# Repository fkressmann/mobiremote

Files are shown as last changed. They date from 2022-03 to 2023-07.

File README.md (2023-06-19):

# MobiRemote

## What

This small tool was built to remote control and monitor a Mobicool FR 40 / MCF 40 (34/60
respectively) fridge. It's somehow inspired
by [this project on GitHub](https://github.com/UnifiedEngineering/mobicool-fr34) which completly
replaces the firmware of the controller. I didn't want to go that far to write my own firmware, I
just wanted the possibility of remote monitoring / control.

## Why

This project is part of my bigger SmartBoat project. I wanted to be able to integrate the fridge and
control the target temperature and on/off state (not just using a relay to turn off power). There
were two main reasons why I wanted to programmatically change the temp:

- According to the outside temperature (nobody needs 2°C beer at 30° outside temp, brain freeze
  coming...)
- The available electrical energy. Cool down during the day when there is a lot of PV energy. Save
  energy and noise at night. Rise temperature / turn off fridge when battery is low.

## How

As the internal logic of the fridge already runs on 3v3, I could use this for the ESP, too.

### Networking

MQTT is used for communication.

#### MQTT out

- ```{prefix}/ip``` IP address of the chip (retained)
- ```{prefix}/rssi``` Signal strength of the WiFi (retained)
- ```{prefix}/log``` Log (retained)
- ```{prefix}/temp``` Current temperature every 1-2sek
- ```{prefix}/target``` Reports back target temperature if set sucessfully
- ```{prefix}/power``` Reports back target temperature if set sucessfully

#### MQTT in

All settings require a number as payload

- ```{prefix}/cmnd/inittemp``` Set current target temperature (only for initialization)
- ```{prefix}/cmnd/initpower``` Set current power state (only for initialization)
- ```{prefix}/cmnd/target``` Set target temperature
- ```{prefix}/cmnd/power``` Set power state (turn on/off fridge)
- ```{prefix}/cmnd/status``` Output all configuration. Payload doesn't matter as long as it's specified

### Pressing buttons

I took the minimum invasive way and automated the four buttons of the fridges control panel using an
optocoupler for each button to simulate button presses. After playing a little with the timing, this
works very good by now. As the software is not getting any feedback of the controller, it needs to
remember the current target temperature. This is why it gets written to the flash after each
change (and loaded on boot, same for the power state). It's not planned to change the temperature
manually from now on.

In the beginning I thought about hijacking the SPI like communication between display panel and main
controller but after hooking up a logic analyser, this seemed too complex. Optocouplers are the
easiest way because the display chip (TM1620B) does some crazy multiplexing on the button inputs.
Didn't want so spend too much time reverse engineering that.

### Measuring temp

<del>
Furthermore, I realized that the fridge uses a 10k NTC for temperature measurement and connected
this one to the ESP, too to measure the inside temperature (previously, I had a DS18B20 inside and a
ribbon cable to through the lid).

Normally, you would use a Steinhart and Hart equation to calculate the temp from the resistance of
the NTC, but this somehow did not work out. So I decided to hook up two DS18B20 sensors, cool the
fridge down to -10°C and let it warm up slowly overnight while logging the mean temp of both
DS18B20 and the ESPs avg voltage reading of 1k samples (beware, read ADC only every 10ms or so,
otherwise WiFi crashes...). After plotting this, the curve was surprisingly linear. So used a linear
approximation which had a error of <0.2°C between 0 and 10°C. Precise enough I'd say :D

I did not disconnect the ADC from the main controller because it is used for controlling the
compressor. Maybe this is the reason why the measured voltage was so far off from what one would
expect from a 10k NTC. Nobody knows exactly what kind of voltage divider Mobicool uses on the main
board.
</del>

Forget this, this is for whatever reason way to unreliable. I ended up mounting a DS18B20 inside the box, using flex 
cables to pass through the hinge and ran wires through the cooling holes. Works way better now.

## Result
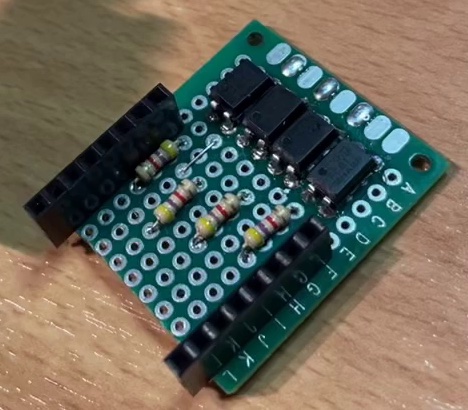
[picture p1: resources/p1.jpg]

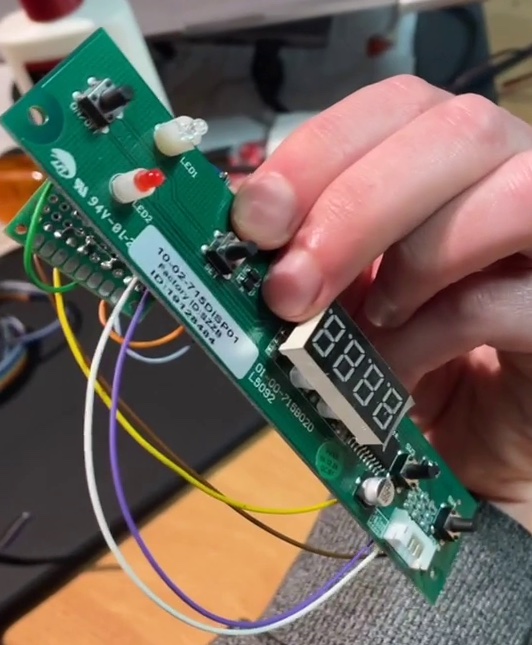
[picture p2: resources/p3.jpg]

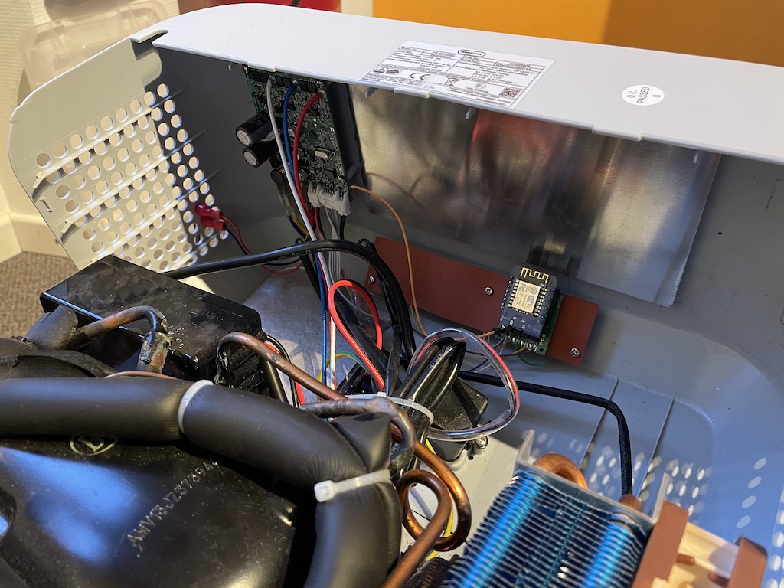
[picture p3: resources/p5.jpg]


## ToDo

- [x] Calibrate temp measurements
- [x] Send temp only when changed
- [x] Use WiFi manager instead of fixed WiFi credentials
- [x] Use WiFi manager to set mqtt settings
- [x] Add some pics here

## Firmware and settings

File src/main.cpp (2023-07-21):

#include <Arduino.h>
#include <ArduinoOTA.h>
#include <EEPROM.h>
#include <ESP8266WiFi.h>
#include <WiFiManager.h>
#include <PubSubClient.h>
#include <OneWire.h>
#include <DallasTemperature.h>
#include <credentials.h>

#define MCF_POWER D6
#define MCF_SET D7
#define MCF_UP D2
#define MCF_DOWN D3
#define BUTTON D5
#define ONE_WIRE_BUS D1
#define LED D4

#define MQTT_SERVER_LABEL "mq_server"
#define MQTT_USER_LABEL "mq_user"
#define MQTT_PASSWORD_LABEL "mq_pw"
#define MQTT_PREFIX_LABEL "mq_pref"

volatile boolean saveConfig = false;
volatile boolean buttonPressed = false;

const char *deviceName = "esp-mobiremote";

const char *topicPower = "power";
const char *topicTargetTemp = "target";
const char *topicIsTemp = "temp";
const char *topicInitTemp = "inittemp";
const char *topicInitPower = "initpower";
const char *topicStatus = "status";

float prevTemp = 0;
struct {
  int tempSet;
  boolean powerState;
  char mqttServer[30];
  char mqttUser[30];
  char mqttPassword[30];
  char mqttPrefix[30];
} config;
String commandPrefix;

WiFiManager wifiManager;

WiFiClient wifiClient;
PubSubClient mqttClient(wifiClient);

OneWire oneWire(ONE_WIRE_BUS);
DallasTemperature DS18B20(&oneWire);

void sendData(String subtopic, String data, bool retained) {
  Serial.println("SENDING: " + subtopic + ":" + data);
  subtopic = config.mqttPrefix + subtopic;
  mqttClient.publish(subtopic.c_str(), data.c_str(), retained);
}

void log(String line) {
  sendData("log", line, true);
}

void sendCurrentTargetTemp() {
    sendData(topicTargetTemp, String(config.tempSet), false);
}

void sendCurrentPowerState() {
    sendData(topicPower, String(config.powerState), false);
}

void sendCurrentTemperature() {
    sendData(topicIsTemp, String(prevTemp), false);
}

void writeConfigToEeprom() {
  EEPROM.begin(sizeof(config));
  EEPROM.put(0, config);
  EEPROM.commit();
  EEPROM.end();
  log("Config " + String(config.tempSet) + ":" + String(config.powerState) + " written to flash.");
}

void reconnectMqtt() {
  if (!mqttClient.connected()) {
    Serial.print("Attempting MQTT connection...");
    // Attempt to connect
    // if you MQTT broker has clientID,username and password
    // please change following line to    if (client.connect(clientId,userName,passWord))
    if (mqttClient.connect(deviceName, config.mqttUser, config.mqttPassword)) {
      Serial.println("connected");
      Serial.println("Subscribing to: " + commandPrefix);
      mqttClient.subscribe((commandPrefix + "/#").c_str());
      sendData("ip", WiFi.localIP().toString(), true);
      sendData("rssi", String(WiFi.RSSI()), true);
    } else {
      Serial.print("failed, rc=");
      Serial.print(mqttClient.state());
      Serial.println(" try again in 1 second");
      delay(1000);
    }
  }
}

void pressButton(int button, boolean longPress) {
  log("Pressing Button " + String(button));
  digitalWrite(button, HIGH);
  delay(200);
  if (longPress) delay(3000);
  digitalWrite(button, LOW);
  delay(100);
}

void pressButton(int button) {
  pressButton(button, false);
}

void changeSetTemperature(int delta) {
  if (delta == 0) {
    return;
  }
  pressButton(MCF_SET);
  if (delta < 0) {
    for (int i = 0; i > delta; i--) {
      pressButton(MCF_DOWN);
    }
  } else {
    for (int i = 0; i < delta; i++) {
      pressButton(MCF_UP);
    }
  }
  // wait for mobicool to exit temperature menu before doing anything else
  delay(11000);
}

void handleNewSetTemp(int newSetTemp) {
  if (!config.powerState) {
    log("Cannot set temp, mobicool is off");
    return;
  }
  if (newSetTemp == config.tempSet || newSetTemp < -10 || newSetTemp > 10) {
    log("Bad newTemp: " + String(newSetTemp) + " (oldTemp: " + String(config.tempSet) + ")");
    return;
  }
  int delta = newSetTemp - config.tempSet;
  changeSetTemperature(delta);
  config.tempSet = newSetTemp;
  writeConfigToEeprom();
  sendCurrentTargetTemp();
}

void handleNewPowerState(boolean newState) {
  if (config.powerState == newState) {
    log("Power is already " + String(newState));
  } else {
    pressButton(MCF_POWER, true);
    config.powerState = newState;
    writeConfigToEeprom();
  }
  sendCurrentPowerState();
}

void handleNtc() {
  DS18B20.requestTemperatures();
  float temp = DS18B20.getTempCByIndex(0);
  if (abs(temp - prevTemp) >= 0.1) {
    prevTemp = temp;
    sendCurrentTemperature();
  }
}

void sendInvalidCommandMessage(char *slashPointer, char *pl) {
  log("Invalid command: " + String(slashPointer) + ":" + String(pl));
}

void callback(char *topic, byte *payload, unsigned int length) {
  digitalWrite(LED, LOW);

  // Parse payload to c string
  char pl[length + 1];
  for (unsigned int i = 0; i < length; i++) {
    pl[i] = payload[i];
  }
  pl[length] = '\0';
  int plInt = atoi(pl);

  char *slashPointer = strrchr(topic, '/');
  if (length == 0) {
    sendInvalidCommandMessage(slashPointer, pl);
  }

  if (strcmp(slashPointer + 1, topicTargetTemp) == 0) {
    handleNewSetTemp(plInt);
  } else if (strcmp(slashPointer + 1, topicInitTemp) == 0) {
    config.tempSet = plInt;
    writeConfigToEeprom();
    sendCurrentTargetTemp();
  } else if (strcmp(slashPointer + 1, topicInitPower) == 0) {
    config.powerState = plInt;
    writeConfigToEeprom();
    sendCurrentPowerState();
  } else if (strcmp(slashPointer + 1, topicPower) == 0) {
    handleNewPowerState(plInt);
  } else if (strcmp(slashPointer + 1, topicStatus) == 0) {
    sendCurrentTemperature();
    sendCurrentTargetTemp();
    sendCurrentPowerState();
  } else {
    sendInvalidCommandMessage(slashPointer, pl);
  }
  digitalWrite(LED, HIGH);
}

void startConfigPortal() {
  WiFi.disconnect();
  ESP.restart();
}

void IRAM_ATTR buttonIsr() {
  buttonPressed = true;
}

void setup() {
  Serial.begin(115200);
  Serial.println();

  attachInterrupt(digitalPinToInterrupt(BUTTON), buttonIsr, FALLING);

  // Read settings from EEPROM
  EEPROM.begin(sizeof(config));
  EEPROM.get(0, config);
  EEPROM.end();
  log("Config " + String(config.tempSet) + ":" + String(config.powerState) + " loaded from flash.");
  Serial.printf("MQTT server: %s \n", config.mqttServer);
  Serial.printf("MQTT user: %s \n", config.mqttUser);
  Serial.printf("MQTT password: %s \n", config.mqttPassword);
  Serial.printf("MQTT prefix: %s \n", config.mqttPrefix);

  WiFi.hostname(deviceName);
  WiFi.persistent(true);

  WiFiManagerParameter p_mqttServer(MQTT_SERVER_LABEL, "MQTT Server", config.mqttServer, 30);
  wifiManager.addParameter(&p_mqttServer);
  WiFiManagerParameter p_mqttUser(MQTT_USER_LABEL, "MQTT User", config.mqttUser, 30);
  wifiManager.addParameter(&p_mqttUser);
  WiFiManagerParameter p_mqttPassword(MQTT_PASSWORD_LABEL, "MQTT Password", config.mqttPassword, 30);
  wifiManager.addParameter(&p_mqttPassword);
  WiFiManagerParameter p_mqttPrefix(MQTT_PREFIX_LABEL, "MQTT Prefix", config.mqttPrefix, 30);
  wifiManager.addParameter(&p_mqttPrefix);

  wifiManager.setConfigPortalTimeout(60);
  
  wifiManager.setSaveConfigCallback([]() {
    Serial.println("Should save config");
    saveConfig = true;
  });

  boolean connected = false;
  while (!connected) {
    connected = wifiManager.autoConnect(STA_SSID, STA_PSK);
  }
  if (saveConfig) {
    strcpy(config.mqttServer, p_mqttServer.getValue());
    strcpy(config.mqttUser, p_mqttUser.getValue());
    strcpy(config.mqttPassword, p_mqttPassword.getValue());
    strcpy(config.mqttPrefix, p_mqttPrefix.getValue());
    writeConfigToEeprom();
    saveConfig = false;
  }

  ArduinoOTA.onStart([]() {
    log("Start OTA update");
  });
  ArduinoOTA.setHostname(deviceName);
  ArduinoOTA.begin();

  pinMode(MCF_POWER, OUTPUT);
  pinMode(MCF_SET, OUTPUT);
  pinMode(MCF_UP, OUTPUT);
  pinMode(MCF_DOWN, OUTPUT);
  pinMode(BUTTON, INPUT_PULLUP);
  pinMode(LED, OUTPUT);
  digitalWrite(LED, HIGH);

  DS18B20.begin();

  commandPrefix = config.mqttPrefix + String("cmnd");
  mqttClient.setServer(config.mqttServer, 1883);
  mqttClient.setCallback(callback);
  reconnectMqtt();

  // Init values in MQTT
  log("Startup complete");
  sendCurrentTargetTemp();
  sendCurrentPowerState();

  Serial.println("Setup finished, looping now");
}

void loop() {
  if (buttonPressed) startConfigPortal();
  ArduinoOTA.handle();
  reconnectMqtt();
  mqttClient.loop();
  if (millis() % 1000 == 0) {
    handleNtc();
  }
}

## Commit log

2022-03-18 Add power state handling
2022-03-19 Read basic temperature
    [Mobicool8266.fzz]
2023-06-19 - Change temperature sensor to DS18B20 cause internal sensor reading was way too unreliable - Add button to delete WiFi config to be able to reconfigure module while known network is near - Update te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
    [Mobicool8266.fzz]
2023-07-21 Run autoconnect as long as it's unsuccessful. Otherwise, the ESP is stuck and needs to be reset manually
    [main.cpp]
